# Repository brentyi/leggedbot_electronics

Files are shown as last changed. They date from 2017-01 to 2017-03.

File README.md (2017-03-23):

# Sparky electrical

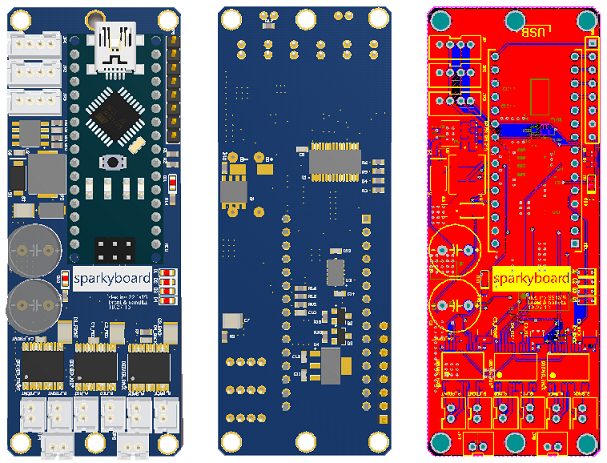
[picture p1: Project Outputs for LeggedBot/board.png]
boards


Repository for the primary control PCB of our hexapedal robot.

Features:
- three TB6612 dual h-bridge driver ICs controlled through a PCA9685 PWM driver (for running 6 individual leg motors)
- an ADXL345 3-axis accelerometer for orientation detection
- an MP1584 5V/3A buck converter (primarily to make powering external devices easy)
- an N-fet-based electronic power switch
- three I2C output connectors for our absolute encoders - these were daisy chained, so we really only needed one
- a filtered battery voltage measurement input

To cut costs and reduce complexity, the board is designed to plug into an ATmega328P-powered Arduino Nano microcontroller.

---

[Demo video](https://www.youtube.com/watch?v=aiBIEI0JHwY) and relevant repositories:
- [firmware](https://github.com/brentyi/sparky_firmware)
- [mechanical design](https://github.com/nanditapiyer/sparky_mechanical)
- [absolute encoder PCB](https://github.com/brentyi/as5048b_breakout)

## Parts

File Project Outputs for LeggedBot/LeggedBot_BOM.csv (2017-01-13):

Comment | Description | Designator | Footprint | Quantity
JST_PH 2 |  | A_BACK, A_FRONT, A_MID, B_BACK, B_FRONT, B_MID, JP4, JP5 | JST-2-PTH-VERT | 8
470uF | Generic electrolytic capacitor w/ 10mm diameter and 5mm pitch | C1, C2 | CAP_10MM | 2
10uF | CAP 10uF 25V -20% to +80% 1210 (3225 Metric) Thickness 1.45mm SMD | C3_BACK, C3_FRONT, C3_MID | CAPC1210(3225)155_N | 3
0.1uF | CAP 100nF 50V ±5% 0603 (1608 Metric) Thickness 1mm SMD | C4_BACK, C4_FRONT, C4_MID, C5, C10, C14 | CAPC0603(1608)100_L | 6
100nF | CAP 100nF 50V ±5% 0603 (1608 Metric) Thickness 1mm SMD | C6 | CAPC0603(1608)100_L | 1
10uF | CAP 10uF 35V ±10% 1210 (3225 Metric) Thickness 2.8mm SMD | C7 | CAPC1210(3225)280_L | 1
150pF | CAP 150pF 50V ±5% 0603 (1608 Metric) Thickness 1mm SMD | C8 | CAPC0603(1608)100_L | 1
22uF | CAP 22uF 6.3V ±10% 1210 (3225 Metric) Thickness 1.7mm SMD | C9 | CAPC1210(3225)170_L | 1
2.2uF | CAP 2.2uF 25V ±10% 0603 (1608 Metric) Thickness 1mm SMD | C11, C12, C13 | CAPC0603(1608)100_L | 3
TLSU1008A(T04) | LED, Red 0603 (1608) 63mCd | D1, D2, D3, D4, D10, D11 | TOSH-0603LED_RED_V | 6
B340A | Surface Mount Schottky Barrier Rectifier, 40 V, 3 A, -55 to 150 degC, 2-Pin SMA, RoHS, Tape and Reel | D5 | DIOD-SMA-2_V | 1
5V TVS | Transient Voltage Suppressor, 6.40 to 231 V, 5 V Stand-off Voltage, Uni-Directional, -55 to 155 degC, 2-pin DO-214AC, Pb-Free, Tape and Reel | D6 | VISH-DO-214AC-2_L | 1
TB6612FNG | Driver IC for Dual DC Motor, 15 V, -20 to 85 degC, 24-Pin SSOP, RoHS, Tape and Reel | DRIVER_BACK, DRIVER_FRONT, DRIVER_MID | TOSH-SSOP-24_M | 3
JST_PH 4 |  | JP1, JP2, JP3 | JST-4-PTH-VERT | 3
1x8 Header |  | JP8 | HEADER 8X1 8.5MM | 1
0630 Inductor | 0630 Inductor | L1 | 0630 INDUCTOR | 1
Arduino Nano |  | MCU | ARDUINO NANO | 1
MOSFET-N | N-Channel MOSFET | Q1 | SOIC127P600X175-8N | 1
BSS138 | N-Channel Logic Level Enhancement Mode Field Effect Transistor, 220 mA, 50 V, -55 to 150 degC, 3-Pin SOT-23, RoHS, Tape and Reel | Q2, Q3 | FAIR-SOT23-3_V | 2
4K7 | 4K7 0.1W 5% 0603 (1608 Metric) SMD | R1, R2 | RESC0603(1608)_L | 2
470R | 470R 0.1W 5% 0603 (1608 Metric) SMD | R3, R4, R5, R6, R14 | RESC0603(1608)_L | 5
10K | 10K 0.1W 5% 0603 (1608 Metric) SMD | R7, R15, R17, R19, R20 | RESC0603(1608)_L | 5
210K | 210K 0.1W 1% 0603 (1608 Metric) SMD | R8, R12 | RESC0603(1608)_L | 2
100K | 100K 0.1W 5% 0603 (1608 Metric) SMD, 100K 0.1W 5% 0603 (1608 Metric) SMD, 100K 0.1W 1% 0603 (1608 Metric) SMD, 100K 0.1W 1% 0603 (1608 Metric) SMD | R9, R11, R16, R18 | RESC0603(1608)_L | 4
40k2 | 40K2 0.1W 1% 0603 (1608 Metric) SMD | R10 | RESC0603(1608)_L | 1
2K2 | 2K2 0.1W 5% 0603 (1608 Metric) SMD | R13 | RESC0603(1608)_L | 1
NXP-PCA9685-SOT361-1 |  | U1 | TSSOP-28 | 1
MP1584 | MP1584 3A, 1.5MHz, 28V Step-Down Converter | U2 | SOIC8E | 1
ADXL345BCCZ-RL7 | 3-Axis, +/-2 g / +/-4 g / +/-8 g / +/-16 g Digital Accelerometer with Digital Output, 1.6 KHz BW, Industrial, 14-pin LGA, Reel | U3 | ADI-CC-14-1_V | 1
TC2117-3.3VDBTR | 800 mA Fixed Low Dropout Positive Regulator, 3-Pin SOT-223, Extended Temperature, Tape and Reel | U4 | SOT-223-DB3_L | 1

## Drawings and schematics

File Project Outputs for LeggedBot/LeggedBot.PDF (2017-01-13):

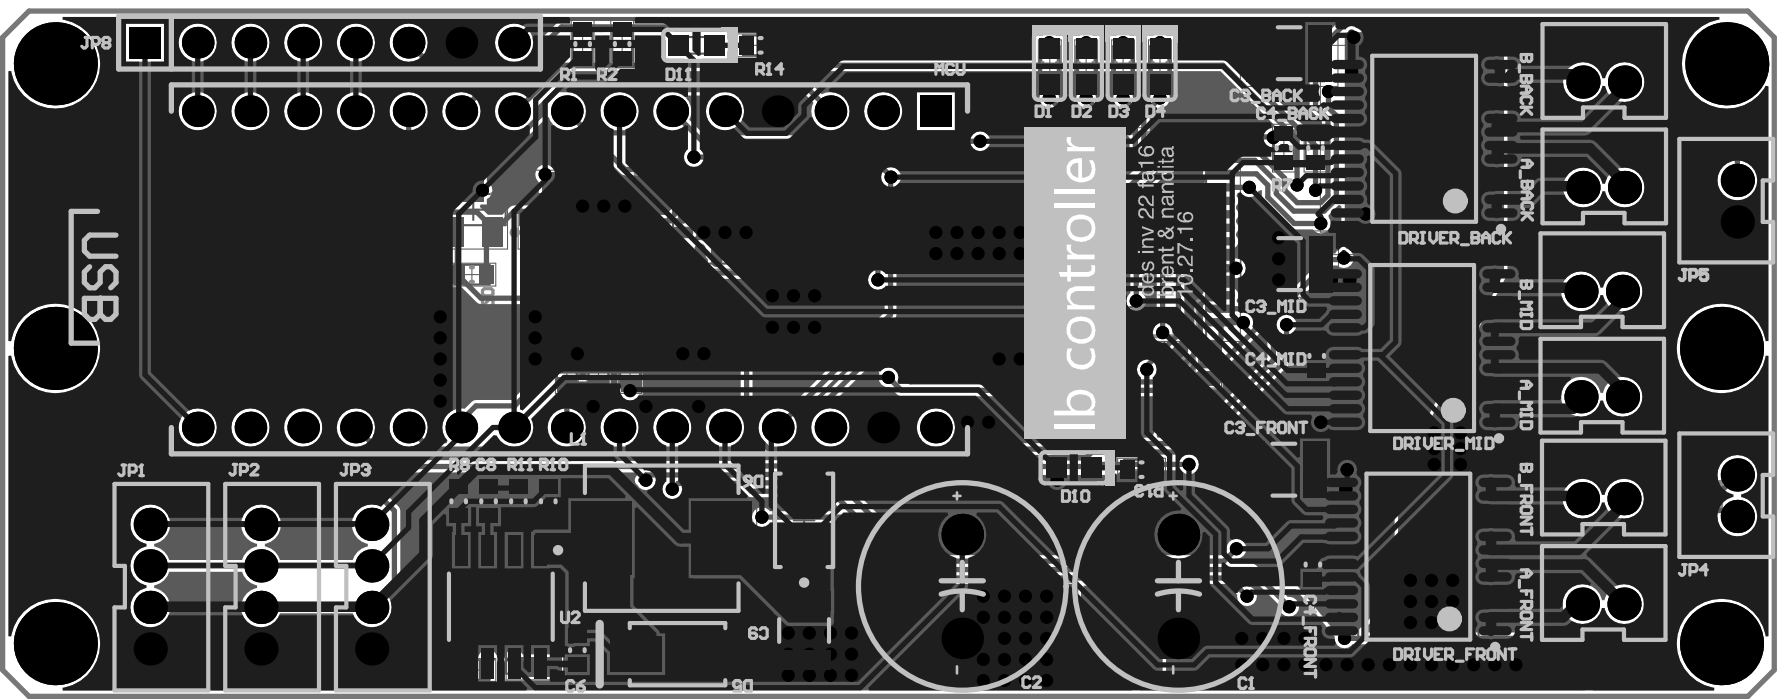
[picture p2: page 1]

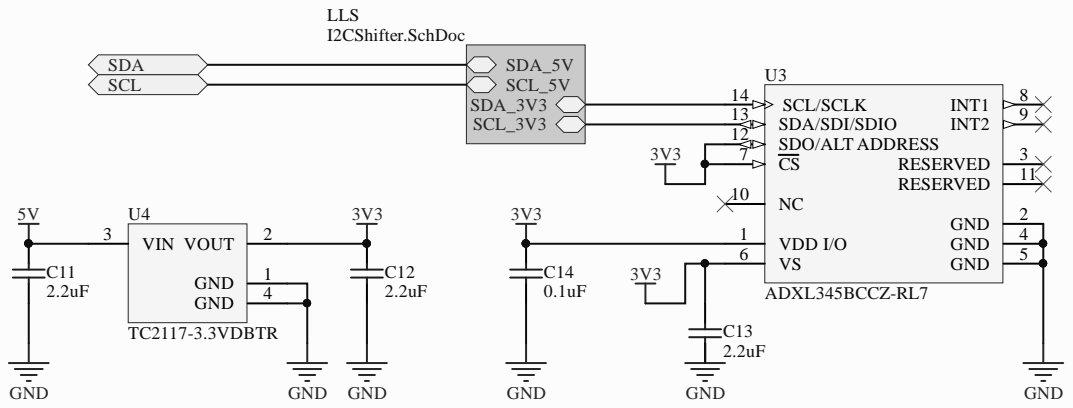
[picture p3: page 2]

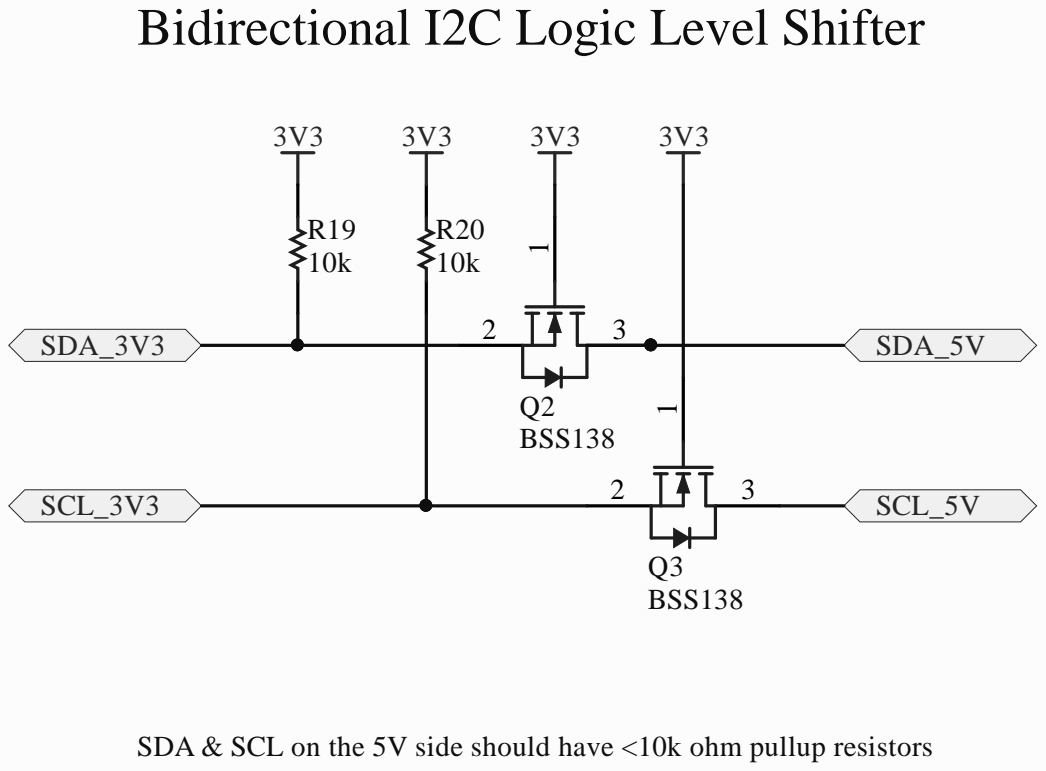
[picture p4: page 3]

Bidirectional I2C Logic Level Shifter

SDA & SCL on the 5V side should have <10k ohm pullup resistors

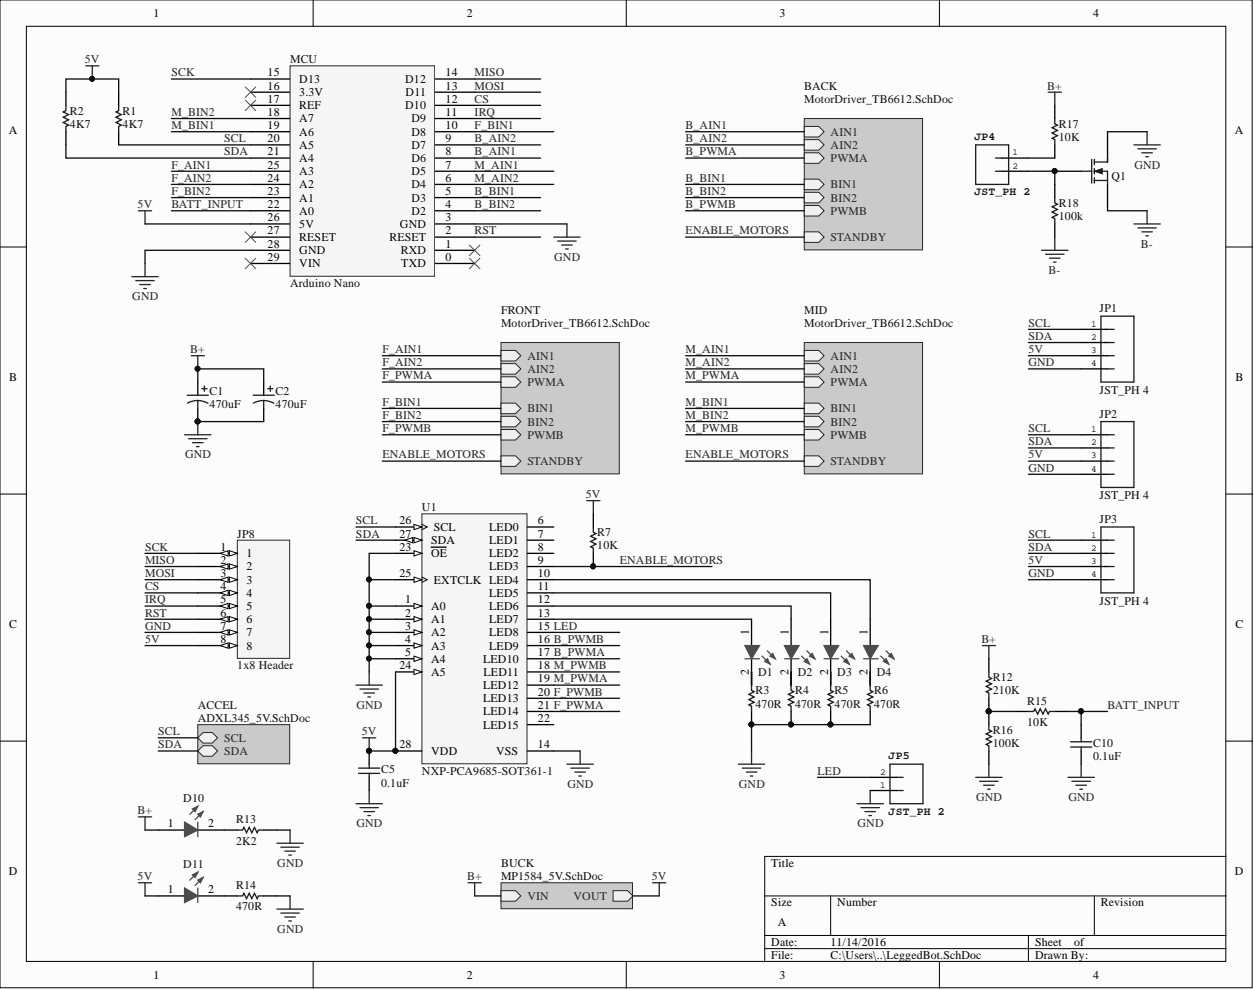
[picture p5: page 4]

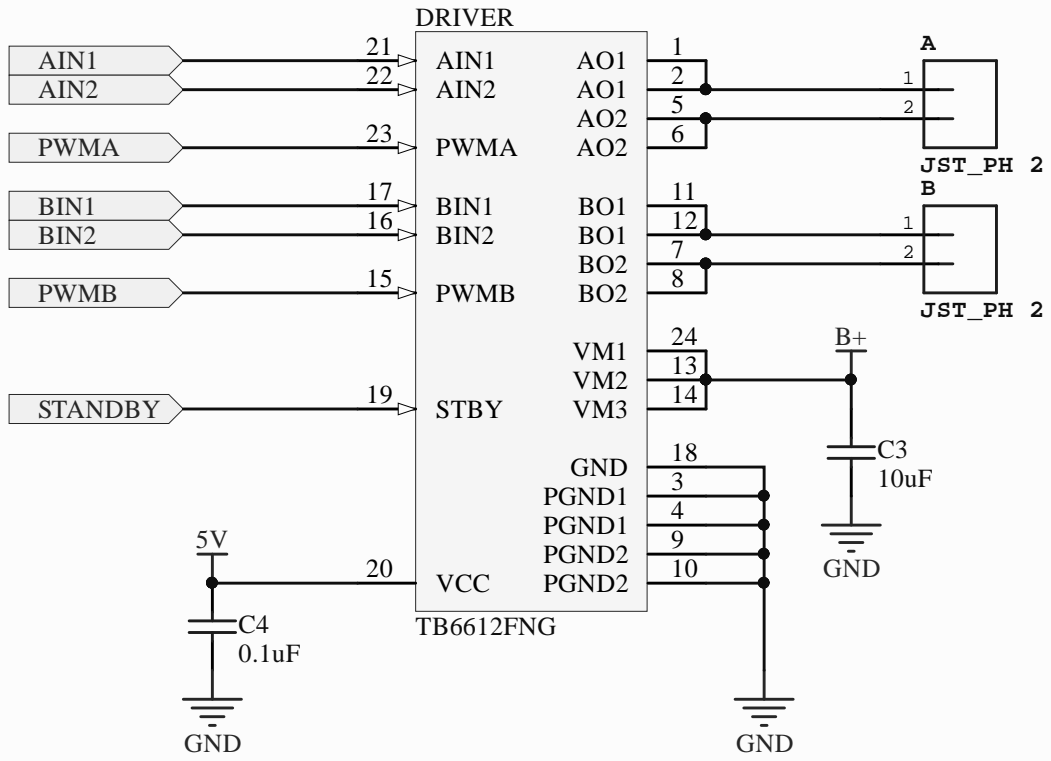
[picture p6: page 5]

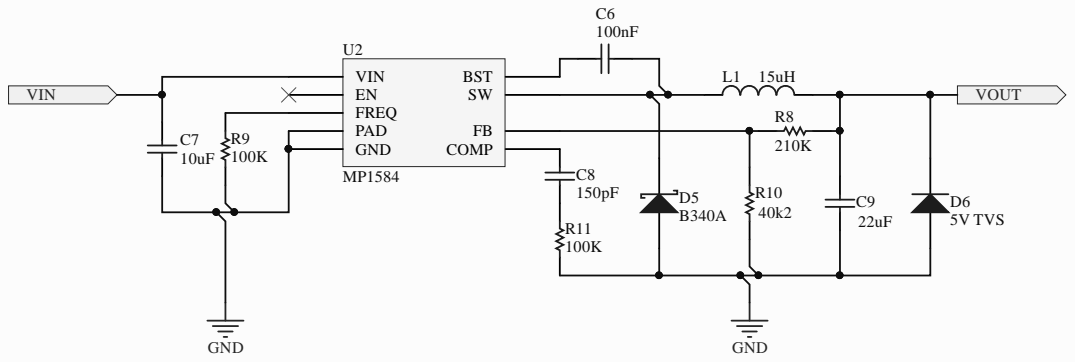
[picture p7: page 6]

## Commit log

2016-10-28 added footprints
    [Footprints.PcbLib]
2016-10-31 added 5v buck converter
    [Components.SchLib, Footprints.PcbLib, LeggedBot.PrjPcb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]
2016-11-05 revision A
    [Footprints.PcbLib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]
2016-11-05 removed undersized vias
    [Footprints.PcbLib]
2016-11-05 better power routing
2016-11-05 added battery voltage monitoring
    [LeggedBot.SchDoc, MP1584_5V.SchDoc]
2016-11-05 added electronic power switch
    [Components.SchLib, Footprints.PcbLib, LeggedBot.SchDoc]
2016-11-06 buck converter rectifier diode polarity fix
    [Footprints.PcbLib, LeggedBot.SchDoc, MP1584_5V.SchDoc]
2016-11-06 misc schematic & layout improvements
    [Footprints.PcbLib, LeggedBot.SchDoc]
2016-11-10 added pdf export
    [LeggedBot.PrjPcb]
2016-11-12 added accelerometer for orientation detection
    [ADXL345_5V.SchDoc, I2CShifter.SchDoc, LeggedBot.SchDoc]
2016-11-13 pwm mux footprint fix
    [Components.SchLib, Footprints.PcbLib, LeggedBot.PrjPcb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]
2016-11-13 hardware i2c, routing fixes, and other neat things
    [Components.SchLib, LeggedBot.SchDoc]
2016-11-14 silkscreen & soldermask tweaks
2017-01-13 minor design tweaks & readme
    [ADXL345_5V.SchDoc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]
